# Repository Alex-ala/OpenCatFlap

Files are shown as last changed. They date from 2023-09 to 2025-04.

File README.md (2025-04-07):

OpenCatFlap
=====

Work in progress...

Being fed up with SurePets cat flap requiring cloud connection to properly work, I decided to design my own flap.
The 3D model is intended to fit into the SurePet adapter already installed.

I want my flap to have at least these features:
1. Easily managable via an API and/or WebUI/MQTT
2. Powered by battery OR power plug!
3. Easy install via AP/Wifi
4. Motion detection on both sides of the flap to check on where a cat is and where it moves to
5. Light barrier that detects into which direction the flap got opened
6. Light barrier in both sides of the "tunnel" to check into which direction the cat moved
7. Independent control of mechanic in and out control. (My cats outsmart SureFlap by letting each other out/in)
8. Two RFID sensors to detect cats on each side and possibly both!
9. Modular design to easily remove the cover, the electronics and the mechanical parts without having to unscrew screws from the outside.

In addition to that the software should be capable of everything SureFlap is capable of, plus:
1. Set pets as "outdoor only"
2. Quickly and more easily set specific per-cat permissions
3. Manually "unlock once" option for each direction

Current state:
------
**Hardware:**

It is bases on an ESP32 (Arduino Nano ESP32 for development) with various sensors and two servos to lock/unlock.
The 3D model is ready to be tested and a printed version is already in use to debug the code. Slight adjustments to the
antenna design will be done in future.

Used vital parts:
- 2x PIR (motion detection): Panasonic AMN33111, testing with cheaper options
- 2x light barrier for flap detection: TCST 1103
- 2x light barrier for tunnel passage: IR LED + NE555 and TSOP18*38 and TSOP18*56
- 2x RFID reader: EM4095
- 2x Servo: DSM44

**Software:**

The software runs a main process that handles global configs and aggregates events reported by the two state machines.
After the last hardware overhaul, quite some work is to be done to update sensors and reading RFID from EM4095 instead of WL-134

## State machines
The locking and unlocking logic is split up into two independent state machines, one for each direction of travel.
One state machine handles the PIR, RFID and Servo on one side of the cat flap.

This way the flap can idependently unlock for ougoing or incoing cats without acidentally opening the other direction aswell, allowing false passages.

Roughly speaking there are 3 states: Idle (only PIR active to wait for motion), Reading (RFID enabled when motion is detected) and unlocked (when a correct RFID is read).

## Wifi

If no Wifi is configured, the flap acts as an AP opening an open "OpenCatFlap" wifi. One can either use this wifi for full control via api, or send credentials to connect to an existing wifi.

## MQTT

MQTT can be configured to connect to an existing MQTT server. The flap will then send events to topics `opencatflap/<flapname>/<type>`.
Configuration via MQTT is planned.

## Webserver

Current means to configure the flap is via http. There is a webserver running on :80 that takes requests to configure wifi, mqtt, lock allowance and cats, aswell as getting some status information.

How to configure (for now):
Wifi: `curl -H "Content-Type: application/json" http://192.168.4.1/api -d '{"command": "wifiConfig", "ssid": "Bockenburg", "passphrase": "", "ntpServer": "ip preffered, hostname possible"}'`
MQTT: `curl -H "Content-Type: application/json" 'http://10.5.0.60/api' -d'{"command": "mqttConfig", "server": "mosquitto.ahome", "port": 8011, "ssl": true, "logActivity": true}'`
MQTT Certificates: 
```
curl -H "Content-Type: text/plain" 'http://10.5.0.60/api/certs?name=key' --data-binary @/home/alex/trash/opencatflap.key
curl -H "Content-Type: text/plain" 'http://10.5.0.60/api/certs?name=cert' --data-binary @/home/alex/trash/opencatflap.crt
curl -H "Content-Type: text/plain" 'http://10.5.0.60/api/certs?name=ca' --data-binary @/home/alex/trash/ca.crt
```

**Future Improvements:**
- NE555 is too inconsistant due to 5% tolerance capacitor with bad temperature coefficient
- Tuning condensators for EM4095 have to be bigger to allow more jiggle-room when building an antenna
- Cheaper connectors for the PCB and external sensors
- Battery backup circuit
- ESP32 directly onboard

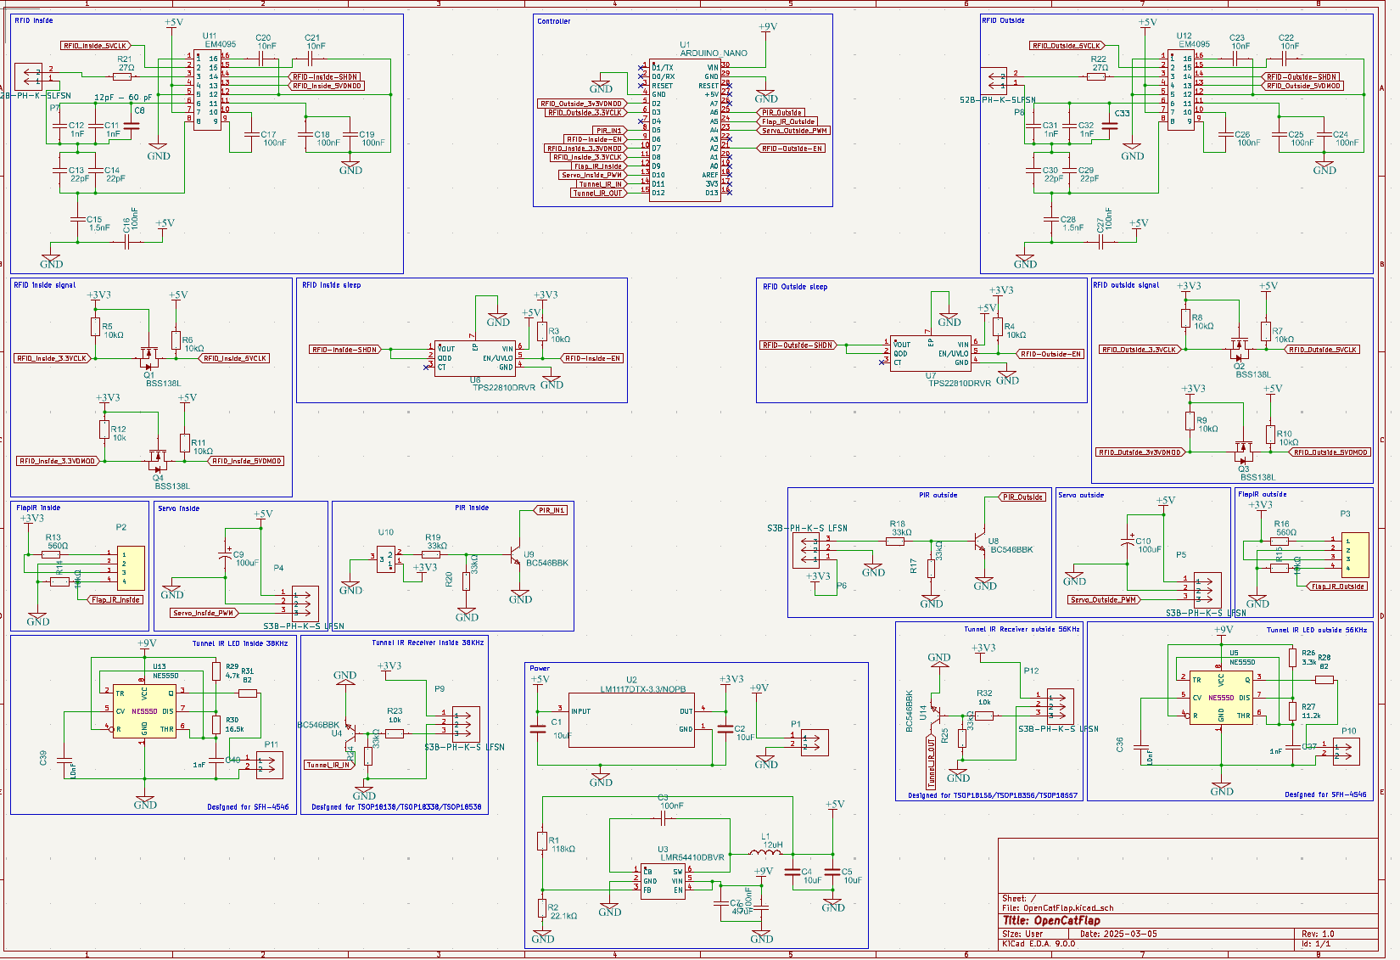
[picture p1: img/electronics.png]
schematics

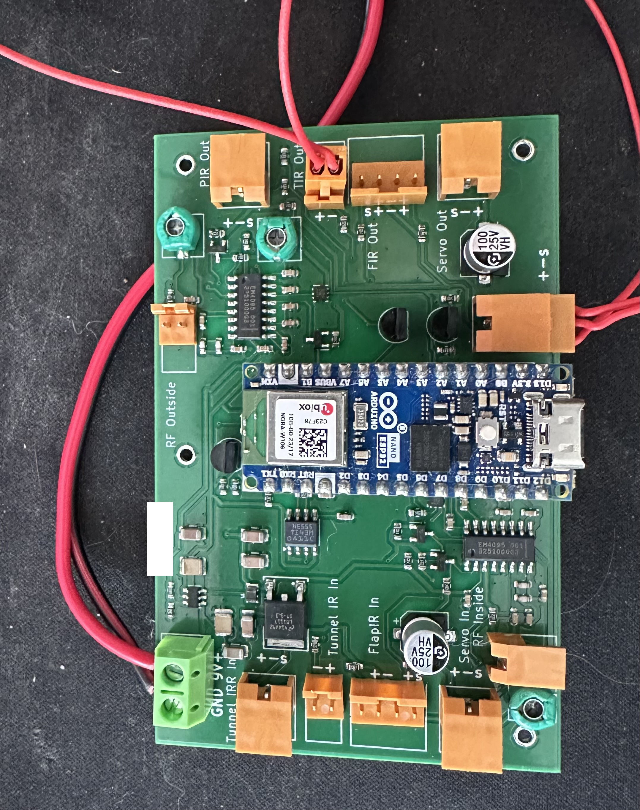
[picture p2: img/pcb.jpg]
pcb


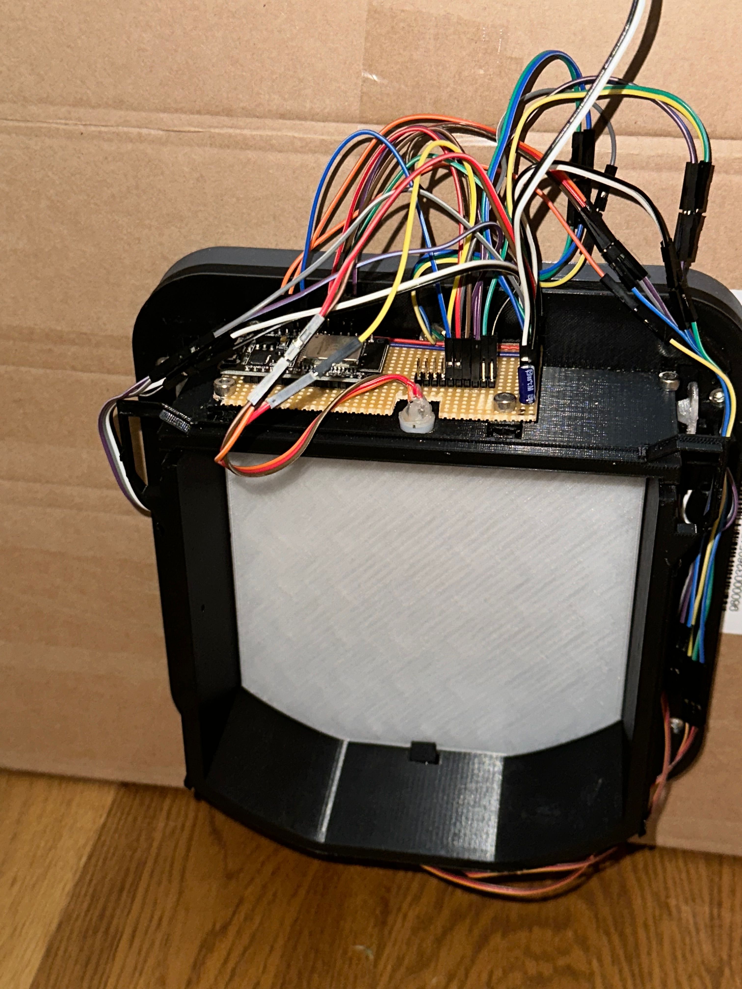
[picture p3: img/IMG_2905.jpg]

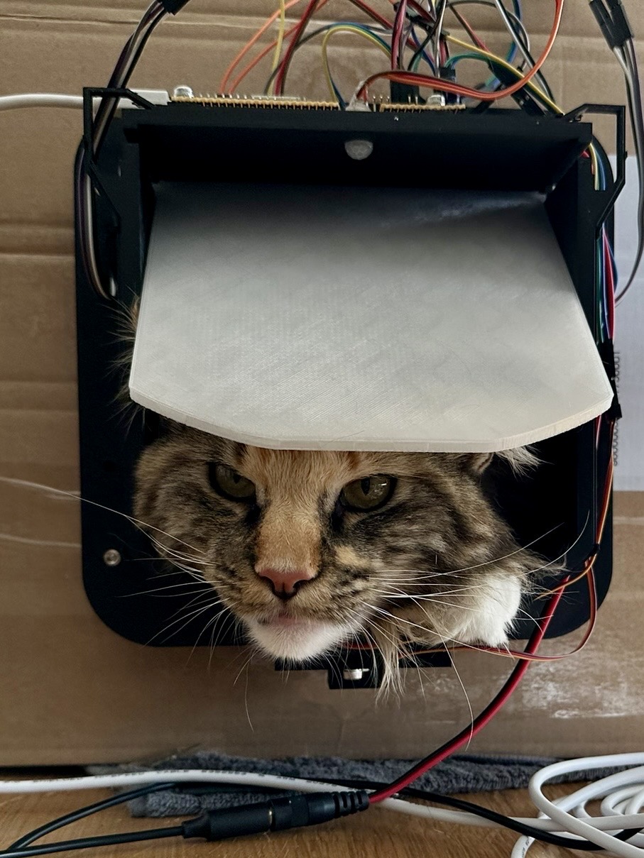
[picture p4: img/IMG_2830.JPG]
cat approved


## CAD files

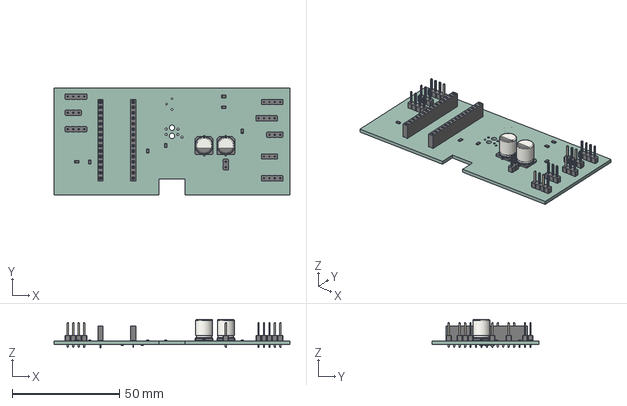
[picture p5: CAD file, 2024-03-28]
cad/opencatflap/opencatflap.step
110.0 x 50.0 x 13.1 mm
OpenCatFlap PCB

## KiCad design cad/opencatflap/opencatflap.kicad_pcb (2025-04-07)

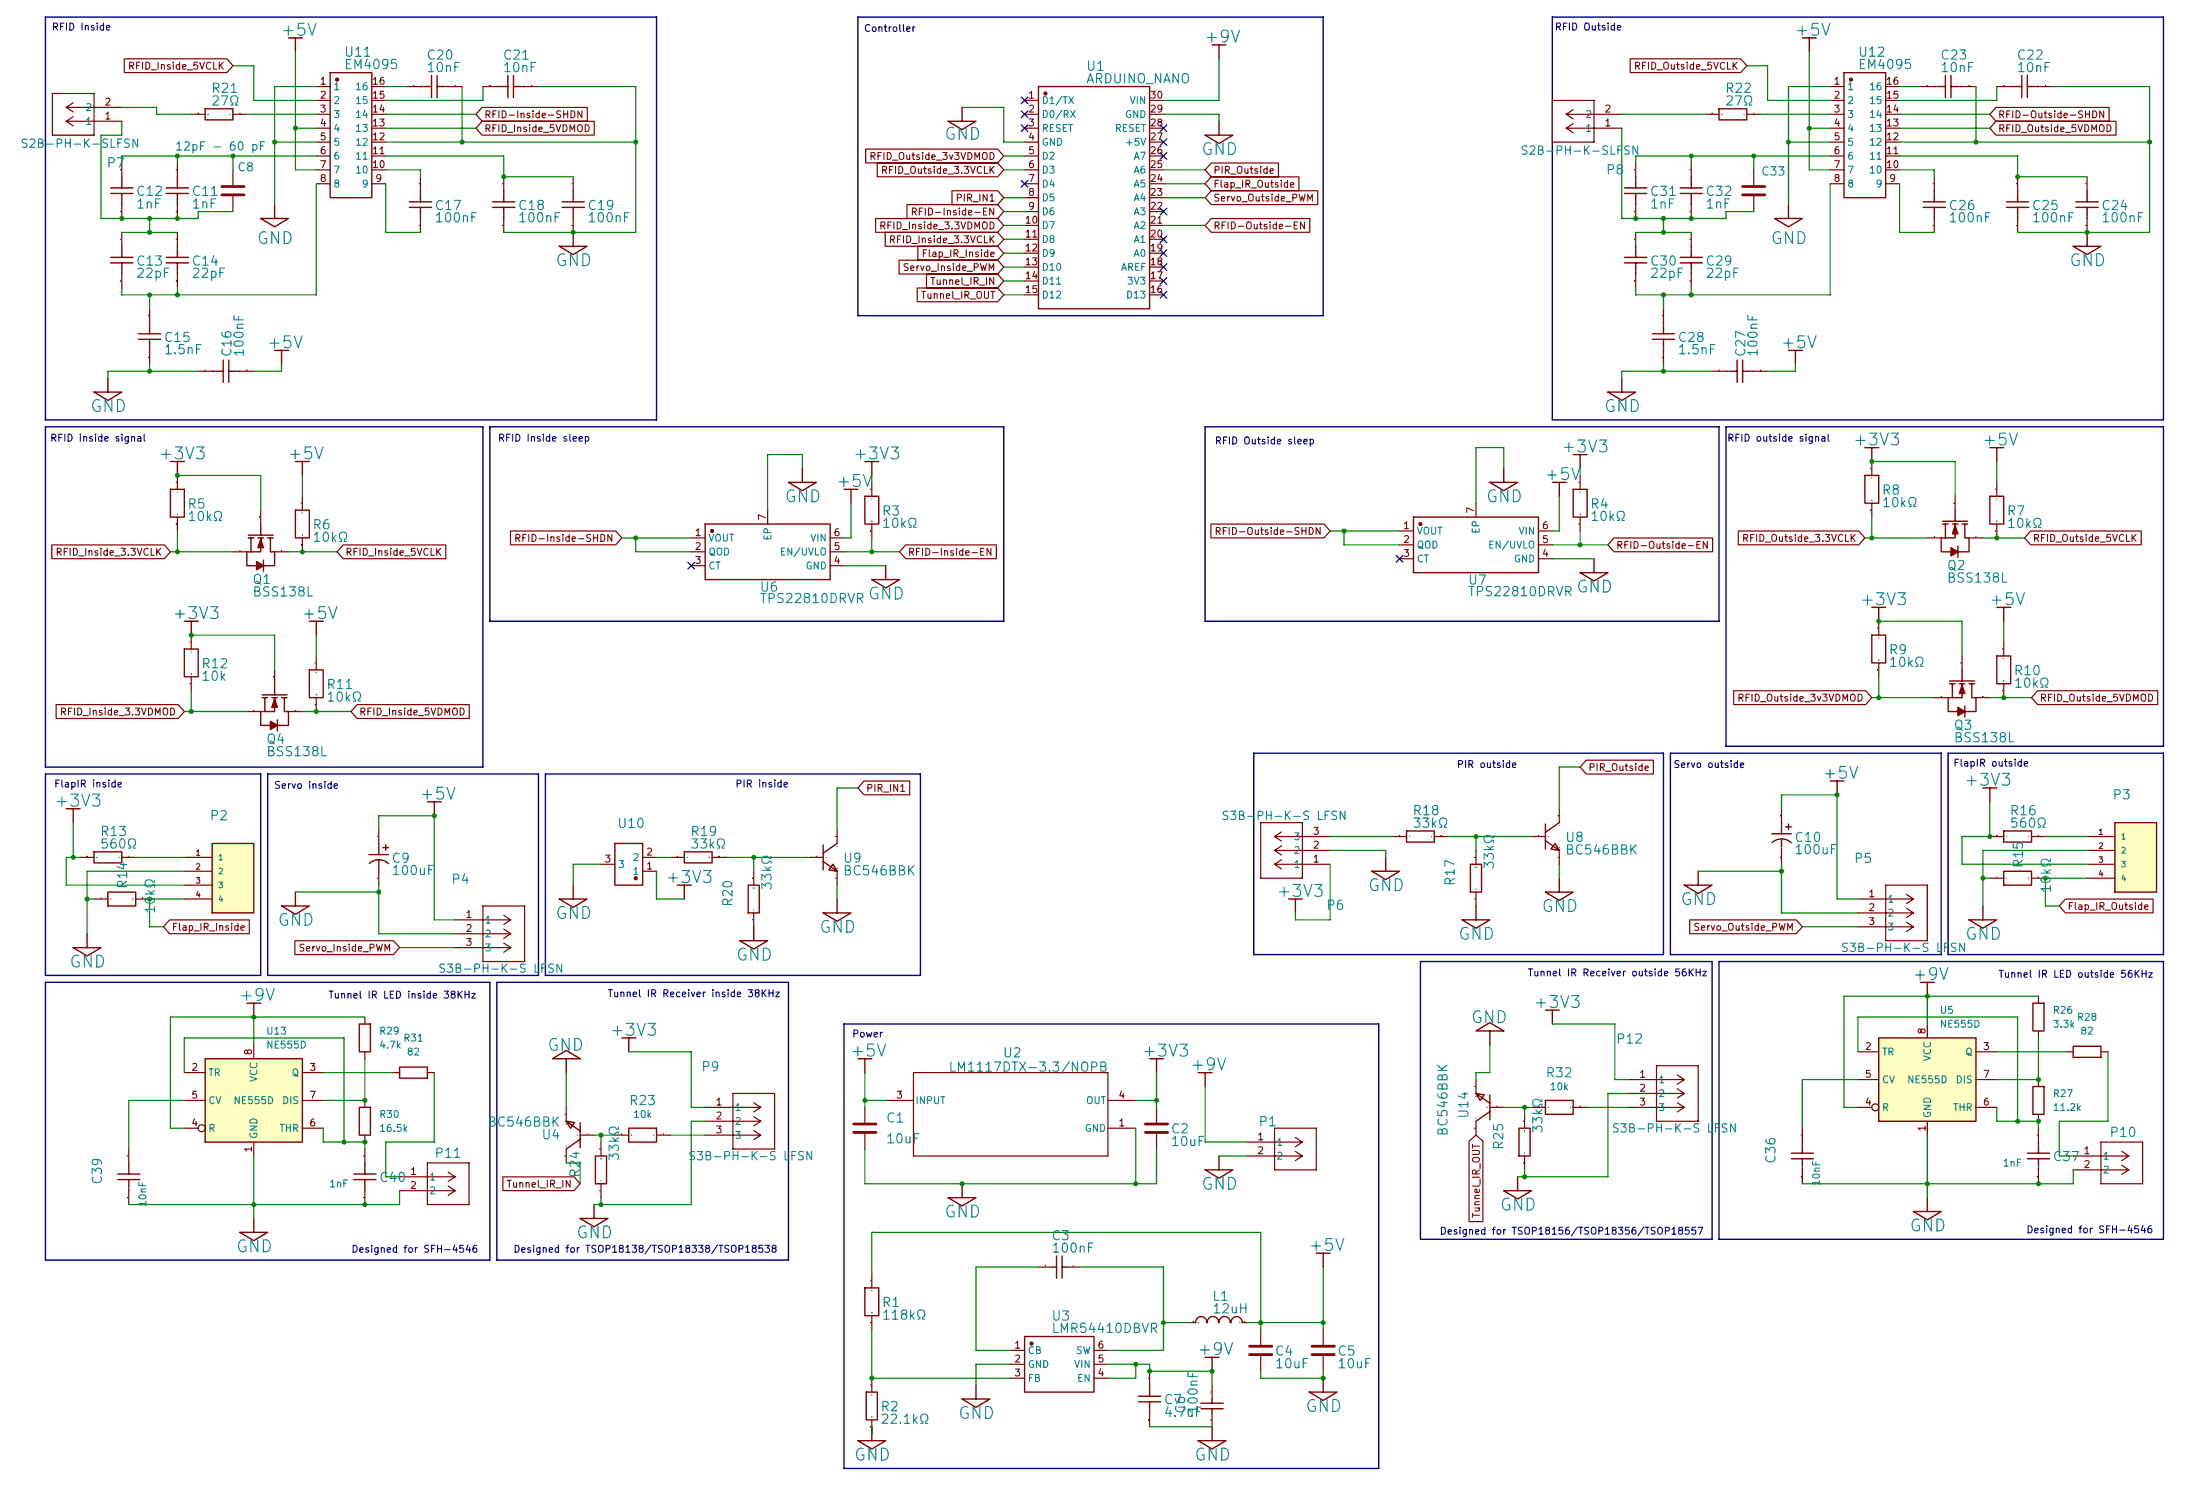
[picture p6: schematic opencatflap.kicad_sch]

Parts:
C1, C2, C4, C5: 10uF; CAP_CL31A_SAM; Manufacturer Part CL31A106MBHNNNE
C3, C6: 100nF; C_1210_3225Metric; Manufacturer Part CC1210KKX7R0BB104
C7: 4.7uF; C_1206_3216Metric; Manufacturer Part CL31B475KPHNNNE
C8, C33: 12pF - 60 pF; VCAP_GKGXXX15_SGM; Manufacturer Part GKG30015
C9, C10: 100uF; CP_Elec_6.3x7.7; Manufacturer Part VH1E101ME077000CE0
C11, C12, C31, C32: 1nF; C_0603_1608Metric; Manufacturer Part CC0603JRX7R9BB102
C13, C14, C29, C30: 22pF; C_0603_1608Metric; Manufacturer Part 0603CG220J500NT
C15, C28: 1.5nF; C_0603_1608Metric; Manufacturer Part CL10B152KB8NNNC
C16, C17, C18, C19, C24, C25, C26, C27: 100nF; C_0603_1608Metric; Manufacturer Part CC0603KRX7R7BB104
C20, C21, C22, C23, C36, C39: 10nF; C_0603_1608Metric; Manufacturer Part CC0603KRX7R7BB103
C37, C40: 1nF; C_0603_1608Metric; Manufacturer Part 0603N102F160CT
L1: 12uH; LBM2016TI20J; Manufacturer Part LBM2016T120J
P1, P7, P8, P11: S2B-PH-K-SLFSN; CONN_S2B-PH-K-S_JST; Manufacturer Part S2B-PH-K-SLFSN
P2, P3: S4B-PH-K-S_LF__SN_; CONN_S4B-PH-K-S_JST; Manufacturer Part S4B-PH-K-S(LF)(SN)
P4, P5, P6, P9, P12: S3B-PH-K-S LFSN; CONN_S3B-PH-K-S_JST; Manufacturer Part S3B-PH-K-S LFSN
P10: IL-G-2P-S3T2-SA; CONN_S2B-PH-K-S_JST; Manufacturer Part S2B-PH-K-SLFSN
Q1, Q2, Q3, Q4: BSS138L; Manufacturer Part BSS138L
R1: 118kΩ; R_0603_1608Metric; Manufacturer Part RT0603FRE07118KL
R2: 22.1kΩ; R_0603_1608Metric; Manufacturer Part RC0603FR-0722K1L
R3, R4, R5, R6, R7, R8, R9, R10, R11, R14, R15: 10kΩ; R_0603_1608Metric; Manufacturer Part RC0603FR-0710KL
R12, R23, R32: 10k; R_0603_1608Metric; Manufacturer Part RC0603FR-0710KL
R13, R16: 560Ω; R_0603_1608Metric; Manufacturer Part AC0603FR-07560RL
R17, R18, R19, R20, R24, R25: 33kΩ; R_0603_1608Metric; Manufacturer Part RC0603FR-0733KL
R21, R22: 27Ω; R_0603_1608Metric; Manufacturer Part RC0603FR-0727RL
R26: 3.3k; R_0603_1608Metric; Manufacturer Part AC0603FR-073K3L
R27: 11.2k; R_0603_1608Metric; Manufacturer Part 0603WAF1122T5E
R28, R31: 82; R_0603_1608Metric; Manufacturer Part RC0603FR-0782RL
R29: 4.7k; R_0603_1608Metric; Manufacturer Part RC0603FR-074K7L
R30: 16.5k; R_0603_1608Metric; Manufacturer Part RC0603FR-0716K5L
U1: ARDUINO_NANO; Arduino Nano ESP32; Manufacturer Part 2x M20-7821546
U2: LM1117DTX-3.3/NOPB; LM1117DTX-3.3NOPB; Manufacturer Part LM1117DTX-3.3/NOPB
U3: LMR54410DBVR; U_SOT-23_TEX; Manufacturer Part LMR54410DBVR
U4, U8, U9, U14: BC546BBK; TO-92L_Inline; Manufacturer Part BC546BBK
U5, U13: NE555D; SOIC-8_3.9x4.9mm_P1.27mm; Manufacturer Part NE555D
U6, U7: TPS22810DRVR; DRV0006A_NV; Manufacturer Part TPS22810DRVR
U10: SENSOR MOTION SPOT 5V BLK LENS; AMN33111; Manufacturer Part AMN33111
U11, U12: EM4095; Manufacturer Part EM4095HMSO16B+

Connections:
+3V3: C2.1, P2.3, P3.3, P6.1, P9.1, P12.1, Q1.1 (G), Q2.1 (G), Q3.1 (G), Q4.1 (G), R3.2, R4.2, R5.2, R8.2, R9.2, R12.2, R13.1, R16.1, U2.4 (OUT), U10.1
+5V: C1.1, C4.1, C5.1, C9.1, C10.1, C16.1, C27.1, L1.2, P4.1, P5.1, R1.2, R6.2, R7.2, R10.2, R11.2, U2.3 (INPUT), U6.6 (VIN), U7.6 (VIN), U11.4, U11.7, U12.4, U12.7
+9V: C6.2, C7.2, P1.1, R26.2, R29.2, U1.30 (VIN), U3.4 (EN), U3.5 (VIN), U5.4 (R), U5.8 (VCC), U13.4 (R), U13.8 (VCC)
Flap_IR_Inside: P2.4, R14.1, U1.12 (D9)
Flap_IR_Outside: P3.4, R15.1, U1.24 (A5)
GND: C1.2, C2.2, C4.2, C5.2, C6.1, C7.1, C9.2, C10.2, C15.1, C16.2, C18.1, C19.1, C20.2, C21.2, C22.2, C23.2, C24.1, C25.1, C27.2, C28.1, C36.1, C37.1, C39.1, C40.1, P1.2, P2.2, P3.2, P4.2, P5.2, P6.2, P9.2, P10.2, P11.2, P12.2, R2.1, R14.2, R15.2, R17.2, R20.2, R24.2, R25.2, U1.4 (GND), U1.29 (GND), U2.1 (GND), U3.2 (GND), U4.3 (E), U5.1 (GND), U6.4 (GND), U6.7 (EP), U7.4 (GND), U7.7 (EP), U8.3 (E), U9.3 (E), U10.3, U11.1, U11.5, U11.12, U12.1, U12.5, U12.12, U13.1 (GND), U14.3 (E); also elsewhere on the board
unnamed: C8.1, C11.1, C12.1, C13.2, C14.2, P7.1
unnamed: C8.2, C11.2, C12.2, U11.6
unnamed: C13.1, C14.1, C15.2, U11.8
unnamed: C17.1, U11.9
unnamed: C17.2, U11.10
unnamed: C18.2, C19.2, U11.11
unnamed: C20.1, U11.16
unnamed: C21.1, U11.15
unnamed: C22.1, U12.15
unnamed: C23.1, U12.16
unnamed: C24.2, C25.2, U12.11
unnamed: C26.1, U12.9
unnamed: C26.2, U12.10
unnamed: C28.2, C29.1, C30.1, U12.8
unnamed: C29.2, C30.2, C31.1, C32.1, C33.1, P8.1
unnamed: C31.2, C32.2, C33.2, U12.6
unnamed: P2.1, R13.2
unnamed: P3.1, R16.2
unnamed: P6.3, R18.2
unnamed: P7.2, R21.1
unnamed: P8.2, R22.1
unnamed: P9.3, R23.2
unnamed: P10.1, R28.2
unnamed: P11.1, R31.2
unnamed: P12.3, R32.2
unnamed: R19.2, U10.2
unnamed: R21.2, U11.3
unnamed: R22.2, U12.3
unnamed: C3.1, U3.1 (CB)
unnamed: R1.1, R2.2, U3.3 (FB)
unnamed: C3.2, L1.1, U3.6 (SW)
unnamed: R23.1, R24.1, U4.2 (B)
unnamed: C36.2, U5.5 (CV)
unnamed: R26.1, R27.2, U5.7 (DIS)
unnamed: R28.1, U5.3 (Q)
unnamed: C37.2, R27.1, U5.2 (TR), U5.6 (THR)
unnamed: R17.1, R18.1, U8.2 (B)
unnamed: R19.1, R20.1, U9.2 (B)
unnamed: C39.2, U13.5 (CV)
unnamed: R29.1, R30.2, U13.7 (DIS)
unnamed: R31.1, U13.3 (Q)
unnamed: C40.2, R30.1, U13.2 (TR), U13.6 (THR)
unnamed: R25.1, R32.1, U14.2 (B)
PIR_IN1: U1.8 (D5), U9.1 (C)
PIR_Outside: U1.25 (A6), U8.1 (C)
RFID-Inside-EN: R3.1, U1.9 (D6), U6.5 (EN/UVLO)
RFID-Inside-SHDN: U6.1 (VOUT), U6.2 (QOD), U11.14
RFID-Outside-EN: R4.1, U1.21 (A2), U7.5 (EN/UVLO)
RFID-Outside-SHDN: U7.1 (VOUT), U7.2 (QOD), U12.14
RFID_Inside_3.3VCLK: Q1.2 (S), R5.1, U1.11 (D8)
RFID_Inside_3.3VDMOD: Q4.2 (S), R12.1, U1.10 (D7)
RFID_Inside_5VCLK: Q1.3 (D), R6.1, U11.2
RFID_Inside_5VDMOD: Q4.3 (D), R11.1, U11.13
RFID_Outside_3.3VCLK: Q2.2 (S), R8.1, U1.6 (D3)
RFID_Outside_3v3VDMOD: Q3.2 (S), R9.1, U1.5 (D2)
RFID_Outside_5VCLK: Q2.3 (D), R7.1, U12.2
RFID_Outside_5VDMOD: Q3.3 (D), R10.1, U12.13
Servo_Inside_PWM: P4.3, U1.13 (D10)
Servo_Outside_PWM: P5.3, U1.23 (A4)
Tunnel_IR_IN: U1.14 (D11), U4.1 (C)
Tunnel_IR_OUT: U1.15 (D12), U14.1 (C)

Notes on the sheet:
FlapIR inside
Tunnel IR Receiver outside 56KHz
FlapIR outside
Designed for TSOP18138/TSOP18338/TSOP18538
Controller
PIR outside
Tunnel IR LED inside 38KHz
Servo outside
Designed for SFH-4546
Designed for TSOP18156/TSOP18356/TSOP18557
RFID Outside
RFID inside signal
RFID Outside sleep
Power
Servo inside
RFID outside signal
PIR inside
RFID Inside
RFID Inside sleep
Tunnel IR LED outside 56KHz
Tunnel IR Receiver inside 38KHz

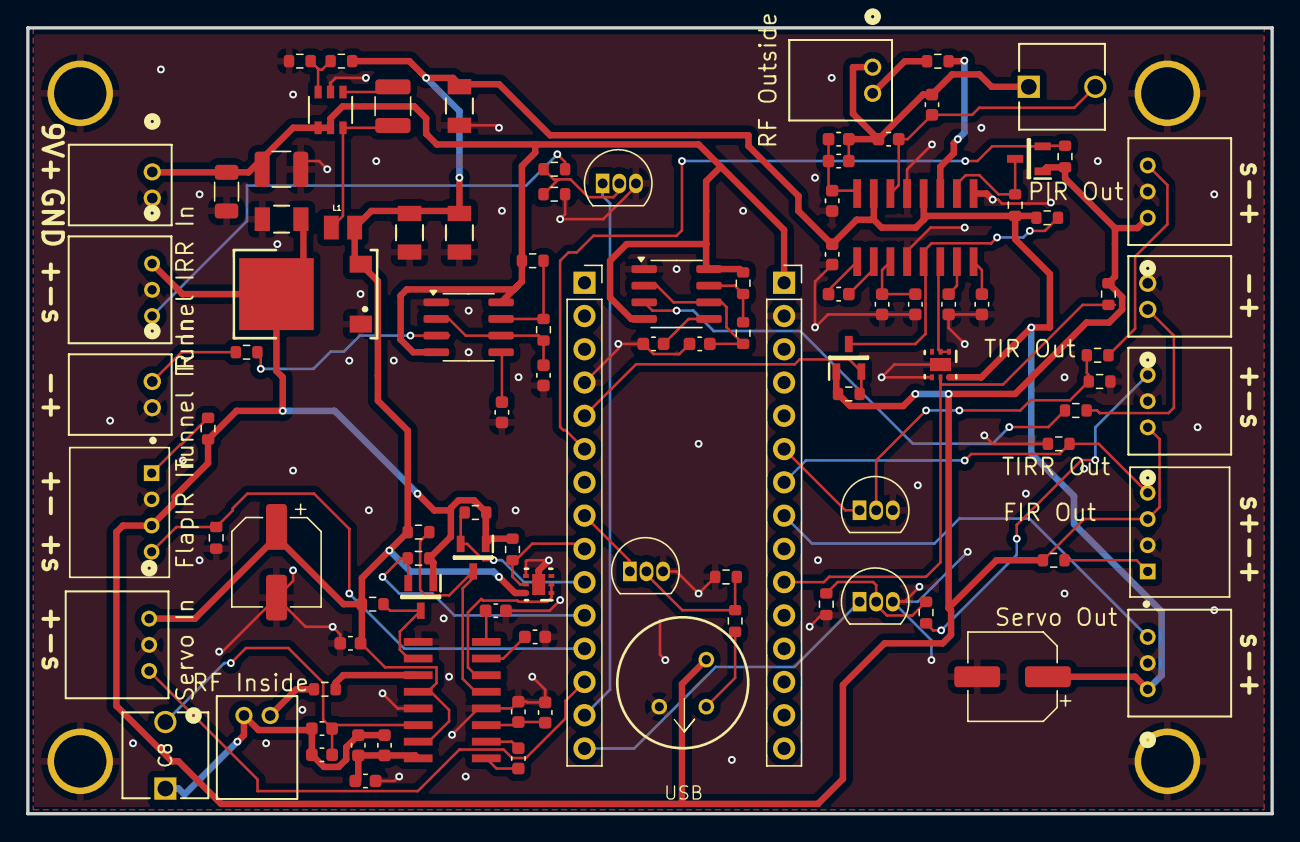
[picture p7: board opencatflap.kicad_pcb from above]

Board: 2 copper layers, 95.0 x 60.0 mm, 104 parts (1 on the bottom side), 67 nets.

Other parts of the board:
Pad_gge19202, Pad_gge19226, Pad_gge19274, Pad_gge19274#2: Bohrloch

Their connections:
GND: Pad_gge19202.1, Pad_gge19226.1, Pad_gge19274.1, Pad_gge19274#2.1; also elsewhere on the board

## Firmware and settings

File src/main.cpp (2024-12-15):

#include <Arduino.h>
#include <OCFFilesystem.h>
#include <OCFWifi.h>
#include <OCFWebserver.h>
#include <OCFFlapControl.h>
#include <OCFMQTT.h>

void setup() {
  Serial.begin(9600);
  Serial.setDebugOutput(true);
  OCFFilesystem::initSPIFFS();
  sleep(20);
  Serial.write("INIT");
  // start flap task
  OCFFlapControl::init();
  xTaskCreate(OCFFlapControl::loop, "flapcontrol", 10000, NULL, 3, NULL);
  // start Wifi monitor task  
  OCFWifi::init();  
  xTaskCreate(OCFWifi::monitorWifi,"monitorwifi", 2500, NULL, 2, NULL);
  // start Webserver task
  OCFWebserver::init();
  xTaskCreate(OCFWebserver::loop, "webserver", 10000, NULL, 2, NULL);
  // // start MQTT monitor task  
  OCFMQTT::init();  
  xTaskCreate(OCFMQTT::monitorMQTT,"monitormqtt",5000,NULL, 2, NULL);
}

void loop() {
}

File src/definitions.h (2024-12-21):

#define OCF_MAX_JSON_SIZE 1500

#define OCF_SERVO_IN_PIN D10
#define OCF_SERVO_IN_LOCKED 35
#define OCF_SERVO_IN_UNLOCKED 64
#define OCF_SERVO_OUT_PIN A4
#define OCF_SERVO_OUT_LOCKED 65
#define OCF_SERVO_OUT_UNLOCKED 30

// TODO: With the new board, PIR is going LOW when motion detected. Also HIGH isnt high enough for digitalRead
#define OCF_MOTION_INSIDE_PIN D5
#define OCF_MOTION_OUTSIDE_PIN A6
#define OCF_MOTION_DELAY 200

// TODO: FlapIR can see through transparent PETG
#define OCF_FLAPIR_OUTSIDE_PIN A5
#define OCF_FLAPIR_INSIDE_PIN D9
#define OCF_FLAPIR_THRESHOLD 1000

#define OCF_TUNNELIR_INSIDE_PIN D4
#define OCF_TUNNELIR_OUTSIDE_PIN A7

#define OCF_RFID_INSIDE_RX D2
#define OCF_RFID_INSIDE_TX D12
#define OCF_RFID_INSIDE_RST D3
#define OCF_RFID_INSIDE_EN A2
#define OCF_RFID_OUTSIDE_RX D7
#define OCF_RFID_OUTSIDE_TX D11
#define OCF_RFID_OUTSIDE_RST D8
#define OCF_RFID_OUTSIDE_EN D6

#define OCF_DEBUG_PIN D20

#define OCF_DEFAULT_NTP_SERVER "pool.ntp.org"

#define OCF_MQTT_CA_PATH "/mqtt_ca"
#define OCF_MQTT_CERT_PATH "/mqtt_cert"
#define OCF_MQTT_KEY_PATH "/mqtt_key"

#define WIFI_CONFIG_FILE "/wifi_configuration.json"
#define MQTT_CONFIG_FILE "/mqtt_configuration.json"
#define CAT_CONFIG_FILE "/cat_configuration.json"
#define FLAP_CONFIG_FILE "/flap_configuration.json"

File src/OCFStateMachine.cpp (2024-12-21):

#include <OCFStateMachine.h>
#include <OCFConfig.h>
#include <OCFMQTT.h>

// TODO: Enable WIFI & MQTT to debug with powersupply
OCFStateMachine::OCFStateMachine(OCFDirection direction) : direction(direction)
{
    OCFLock::enableServo(direction);
    sleep(1);
    OCFLock::disableServo(direction);
    servoAttached = false;
    lastMotion = 0;
    lastRFID = 0;
    rfidReading = false;

    if (direction == OCFDirection::IN)
    {
        pin_motion = OCF_MOTION_OUTSIDE_PIN;
        // Current hardware build has outside and inside antennas swapped....
        pin_rfid_power = OCF_RFID_OUTSIDE_EN;
        pin_rfid_read = OCF_RFID_OUTSIDE_RX;
        pin_rfid_write = OCF_RFID_OUTSIDE_TX;
        pin_rfid_reset = OCF_RFID_OUTSIDE_RST;
        serial = &Serial1;
        prefix = "In:";
    }
    else if (direction == OCFDirection::OUT)
    {
        pin_motion = OCF_MOTION_INSIDE_PIN;
        pin_rfid_power = OCF_RFID_INSIDE_EN;
        pin_rfid_read = OCF_RFID_INSIDE_RX;
        pin_rfid_write = OCF_RFID_INSIDE_TX;
        pin_rfid_reset = OCF_RFID_INSIDE_RST;
        serial = &Serial2;
        prefix = "Out:";
    }
    pinMode(pin_motion, INPUT_PULLUP);
    digitalWrite(pin_rfid_power, LOW);
    digitalWrite(pin_rfid_reset, HIGH);
    pinMode(pin_rfid_power, OUTPUT);
    pinMode(pin_rfid_reset, OUTPUT);
    serial->begin(9600, SERIAL_8N2, pin_rfid_read, pin_rfid_write);
    currentState = OCFMachineStates::IDLE;
    log_d("%s StateMachine initialized", prefix);
}

void OCFStateMachine::flushRFID(){
    while(serial->available() > 0){
        serial->read();
    }
}

void OCFStateMachine::resetRFID()
{
    log_d("%s reset RFID", prefix);
    flushRFID();
    lastRead = millis();
    rfidReading = false;
    digitalWrite(pin_rfid_reset, LOW);
    delay(10);
    digitalWrite(pin_rfid_reset, HIGH);
}

unsigned long long OCFStateMachine::readRFID()
{
    if (serial->available() == 0) return 0;
    if (serial->available() >= 1 && !rfidReading)
    {
        char input[1];
        input[0] = 0x0;
        while (serial->available())
        {
            serial->read(input, 1);
            if (input[0] == 0x02)
            {
                rfidReading = true;
                log_d("%s Received RFID header", prefix);
                break;
            }
        }
        return 0;
    }
    log_d("%s Reading RFID...", prefix);
    //900 215007389064
    // 38 38 35 36 30 37 46 30 32 33 - 34 38 33 30 - 31 - 31 - 30 30 30 30 - 37 30 32 42 31 30 - 0A F5 03
    // 38 38 35 36 30 37 46 30 32 33 -> Reverse -> 33 32 30 46 37 30 36 35 38 38 -> ASCII -> 320F706588 -> int -> 215007389064
    // 34 38 33 30 -> Reverse -> 30 33 38 34 -> ASCII -> 0384 -> int -> 900
    // try to read tag id
    if (serial->available() < 29)
        return 0;
    serial->readBytes(rfidTag, 29);
    char tag_country_bytes[5];
    char tag_id_bytes[11];
    for (int i = 9; i >= 0; i--)
    {
        tag_id_bytes[9 - i] = rfidTag[i];
    }
    tag_id_bytes[10] = 0x0;
    for (int i = 3; i >= 0; i--)
    {
        tag_country_bytes[3 - i] = rfidTag[10 + i];
    }
    tag_country_bytes[4] = 0x0;
    unsigned long long tag_id = strtoull(tag_id_bytes, NULL, 16);
    long tag_country = strtoul(tag_country_bytes, NULL, 16);
    serial->read();
    for (int x = 0; x < 29; x++)
        rfidTag[x] = 0x0;
    rfidReading = false;
    lastRFID = millis();
    lastRead = lastRFID;
    return tag_id;
    //TODO: tag read wrong
}

void OCFStateMachine::update()
{
    if (currentState == OCFMachineStates::IDLE)
        updateIdle();
    else if (currentState == OCFMachineStates::READING)
        updateReading();
    else if (currentState == OCFMachineStates::UNLOCKED)
        updateUnlocked();
}

void OCFStateMachine::updateIdle()
{
    bool motion = digitalRead(pin_motion) == LOW;
    if (!motion)
        return;
    lastMotion = millis();
    transitionIdleToReading();
}

void OCFStateMachine::updateReading()
{
    bool motion = digitalRead(pin_motion) == LOW;
    if (motion) {
        lastMotion = millis();
    }
    // Return to Idle
    if (lastMotion <= millis() - 10000)
        transitionReadingToIdle();
    // Reset RFID after 5s
    if (lastRead <= millis() - 2000)
        resetRFID();
    // Read until init byte is received
    unsigned long long id = readRFID();
    if (id == 0)
        return;
    if (checkTag(id)) transitionReadingToUnlocked();
}

void OCFStateMachine::updateUnlocked()
{
    bool motion = digitalRead(pin_motion) == LOW;
    if (motion) {
        lastMotion = millis();
    }
    if (lastRFID <= millis() - 5000)
        transitionUnlockedToReading();
    if (lastRead <= millis() - 2000)
        resetRFID();
    long long tag = readRFID();
    if (tag != 0 && !checkTag(tag)) transitionUnlockedToReading();
}

void OCFStateMachine::transitionIdleToReading()
{
    OCFLock::enableServo(direction);
    servoAttached = true;
    rfidReading = false;
    lastRFID = 0;
    lastRead = 0;
    flushRFID();
    digitalWrite(pin_rfid_power, HIGH);
    resetRFID();
    currentState = OCFMachineStates::READING;
    log_d("%s Transition to Reading", prefix);
}

void OCFStateMachine::transitionReadingToIdle()
{
    OCFLock::disableServo(direction);
    servoAttached = false;
    rfidReading = false;
    lastMotion = 0;
    lastRFID = 0;
    lastRead = 0;
    digitalWrite(pin_rfid_power, LOW);
    flushRFID();
    currentState = OCFMachineStates::IDLE;
    log_d("%s Transition to Idle", prefix);
}

void OCFStateMachine::transitionReadingToUnlocked()
{
    resetRFID();
    OCFLock::unlock(direction);
    digitalWrite(pin_rfid_power, HIGH);
    currentState = OCFMachineStates::UNLOCKED;
    log_d("%s Transition to Unlocked", prefix);
    OCFMQTT::sendMessage("state", "unlocked");
}

void OCFStateMachine::transitionUnlockedToReading()
{
    resetRFID();
    OCFLock::lock(direction);
    currentState = OCFMachineStates::READING;
    log_d("%s Transition to Reading", prefix);
    OCFMQTT::sendMessage("state", "locked");
}

OCFMachineStates OCFStateMachine::getState(){
    return currentState;
}
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

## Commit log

2023-06-04 debug motion sensors
2023-06-17 Better value for inside servo
2023-07-08 add bad schematics
2023-09-10 add cad
    [OpenCatFlap.kicad_pcb, OpenCatFlap.kicad_sch]
2023-10-15 Revert "meow"
    This reverts commit 70150f40207d0a9de3da7c8185f4e8c8306b4b66.
    [OpenCatFlap v141.f3d, OpenCatFlap.csv, OpenCatFlap.f3d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]
2024-01-03 Fix wiring
    [OpenCatFlap.kicad_pcb]
2024-03-28 board v2
    [OpenCatFlap.kicad_pcb, OpenCatFlap.kicad_sch, OpenCatFlap.step]
2024-03-28 update schematics
    [OpenCatFlap.kicad_sch]
2024-07-06 Run on new mainboard
    [partitions.csv]
2024-07-07 test rfid, update cad
    [OpenCatFlap v141.f3d, OpenCatFlap.f3d, OpenCatFlap.kicad_pcb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]
2024-12-14 wörk
    [opencatflap.kicad_pcb]
2024-12-15 mqtt, fix rfid logging, add html config
    [OCFStateMachine.cpp, OCFWebserver.cpp, definitions.h]
